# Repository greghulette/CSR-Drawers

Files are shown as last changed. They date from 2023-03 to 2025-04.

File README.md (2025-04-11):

# Horizontal Drawers for the COM-8 CSR Frame

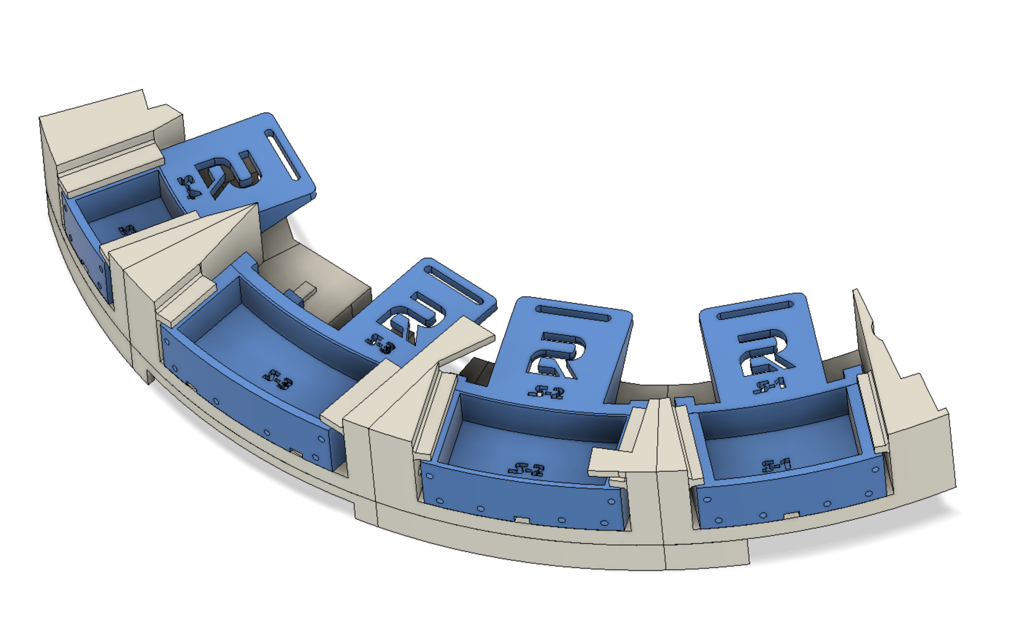
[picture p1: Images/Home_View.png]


 Drawers for the horizontal body panels.  I designed this for the COM-8 CSR frame.  It can be mounted to the frame, or to the skins.  

 I have included the STL's and the Fusion 360 file that you can open and edit anything you'd like.  Each drawer is split up into 4 parts.  
 1. Drawer Holder
 2. Drawer Body
 3. Drawer Servo Arm Attachment
 4. Skin Mount(Optional if you are mounting it to the skin instead of the frame)

 Hardware Needed:
 1. ES08MA II Servos - Qty:4 - [Link](https://www.amazon.com/dp/B07RRWYXL9?psc=1&ref=ppx_yo2ov_dt_b_product_details)  (HITEC HS65 will also work but the standard servo arms that come with them are not long enough.  You will need to get longer arms.Somthing longer than 20mm.  The hole needs to be about 18mm from the pivot point.)
 2. #0-80 5/8" Screws - Qty: 4
 3. #0-80 nuts - Qty: 8
 4. M3x10mm screws - Qty: 6
 5. M3 pressed/heated inserts - Qty: 6  (I also use thse to mount to my frame so I used 11 in total)
 6. 10x5x2mm neodynium N48 Magnets - Qty: 88 - [Link](https://www.amazon.com/dp/B0B6PBXBVJ?psc=1&ref=ppx_yo2ov_dt_b_product_details)
 7. M3x10 tapered screws - Qty: 5 (Only used if you are using the pressed inserts to mount the drawers to the frame)
 8. #4-40 1/2" tapered flat head screw (optional for skirt mount) - Qty 7
 9. #4-40 Lock nuts (optional for skirt mount) - Qty 7

I cut the longest servo arm that came with the servos.  This is the doublesided one.  I cut one side of it off.  I then drilled out the middle hole with a 1/16" drill bit to allow the bolt to go through.  

I put 2 nuts on each of the #0-80 screws and tightened them against each other to prevent the nut from coming loose.  
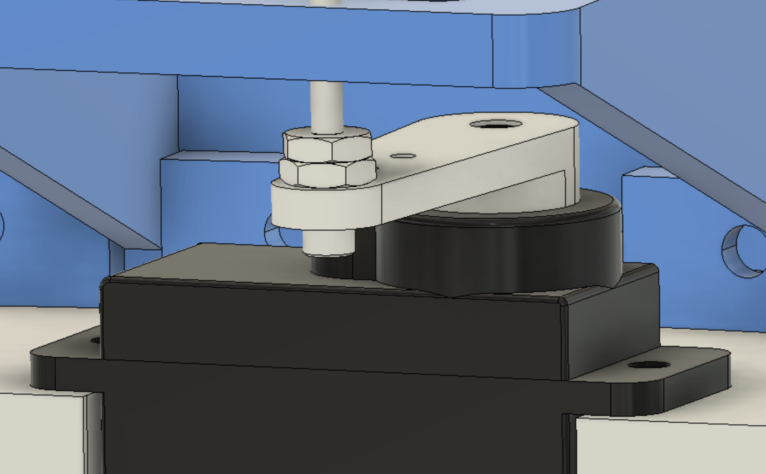
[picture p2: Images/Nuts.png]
Nuts


I used a soldering iron and pressed in the inserts to the side of each holder.  
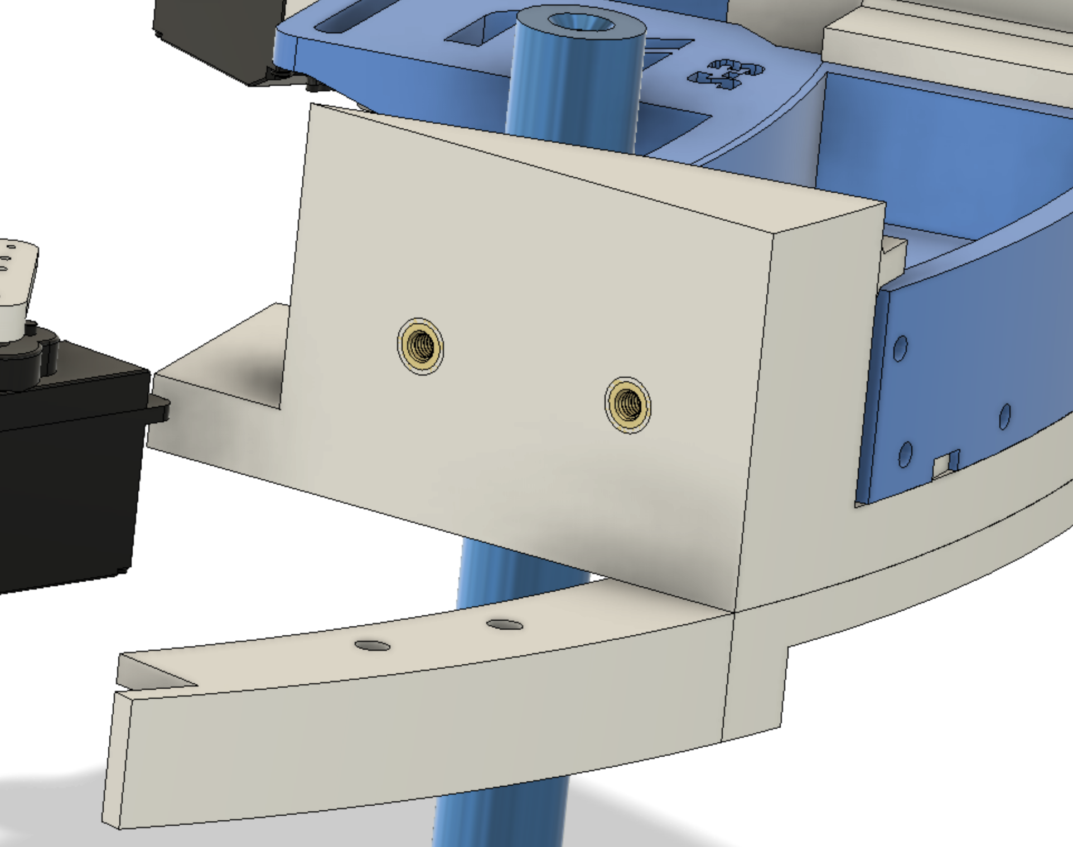
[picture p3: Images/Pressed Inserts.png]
Inserts


I then sanded the sides of each of the holders to make sure they sit flush with each other. Sometimes the pressing of the inserts leaves extra plastic stickup up and any if the sides aren't completely flush, it can cause the alignment to be off.  

You can then screw them together with the M3x10 screws(Not the tapered head ones)
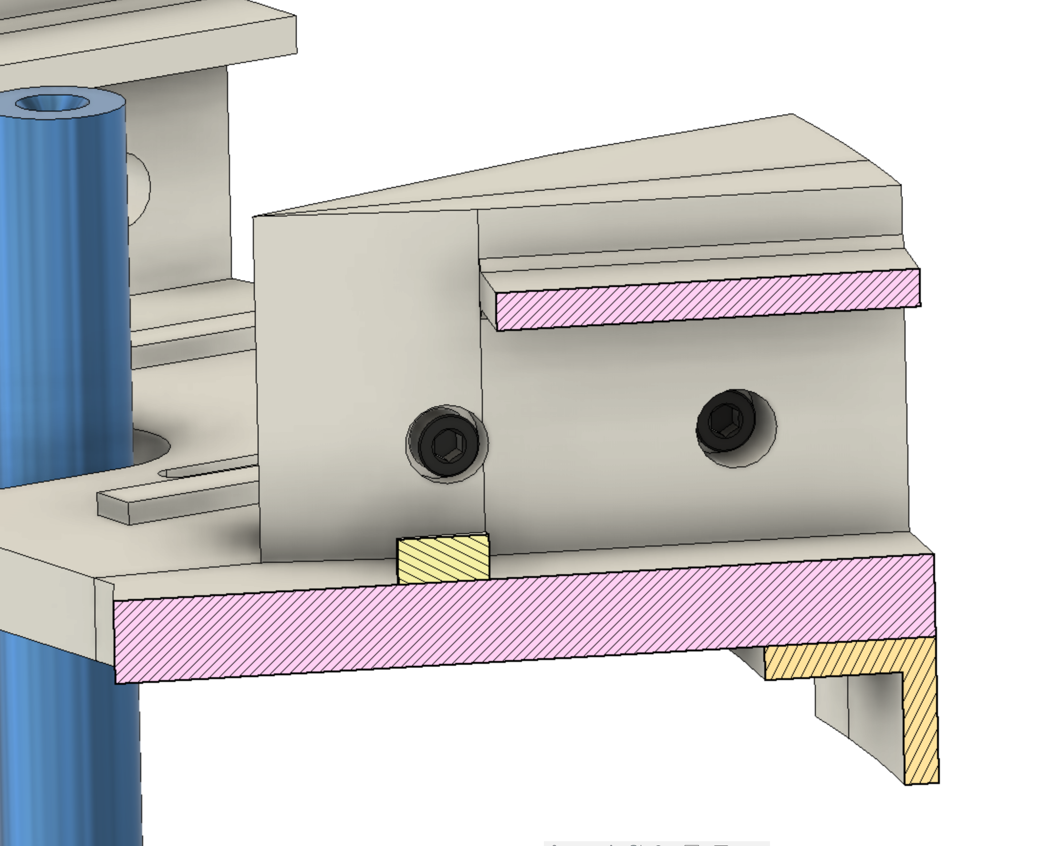
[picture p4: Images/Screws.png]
screws


I sanded the bottom of the drawrers and the top of the holders where the drawers sit on and slide to make sure the drawers slide smoothly.  With 3D printing, the top layer is rarely very smooth and likely has some variations.
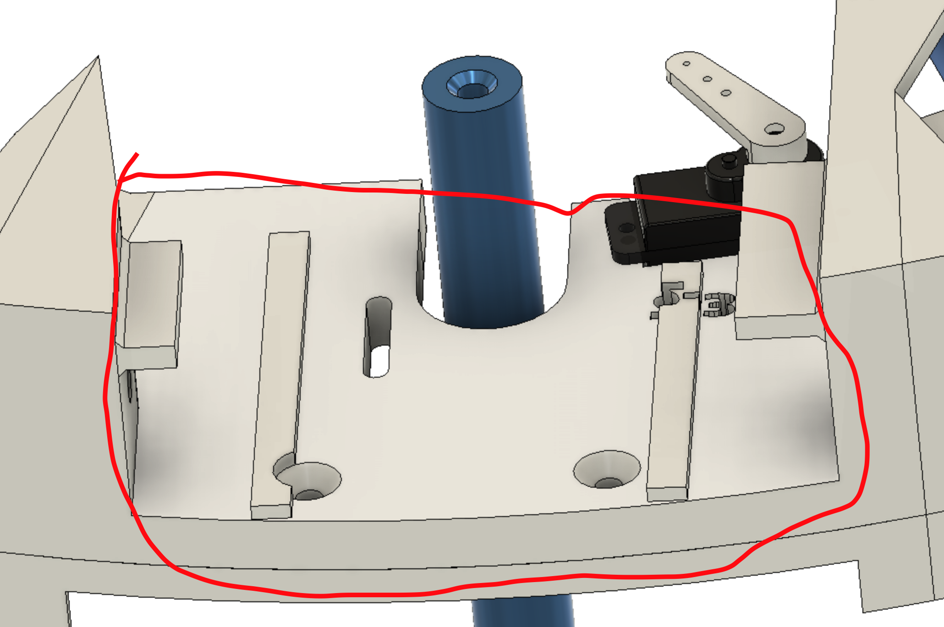
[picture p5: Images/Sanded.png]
sanded


I sanded the bottom of the drawer guides on the holders that stick out to prevent the drawers from lifting up.
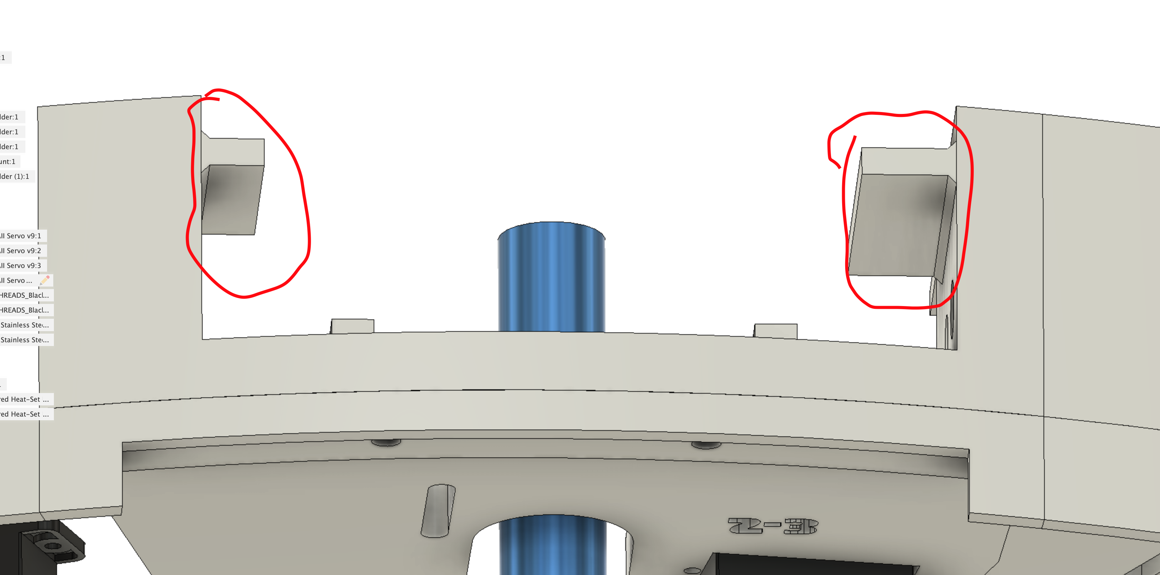
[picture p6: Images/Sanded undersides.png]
Sanded Undersides


THere are holes in the drawers behind the magnets for 2 purposes.  1 is to allow you to get the magnets out if you need to by poking it out from the back, and the 2nd is to allow a place for the glue to go when gluing in the magnets.  I found it easier to put all the magnets in the servo arm attachement first.  Then I placed the magnets for the body onto the magnets in the servo arm attachment and push them in into the body and twised the servo arm attachment away leaving the magnets with the correct polarity in the drawer body.  This helped not only assure the polarity is correct, but also helped me insert the magnets without twisting them.

## Installing on the frame

This seciton is going to sound like I'm rambling on, but this is the way I did it.  

I started off by removing the skins and all the utility arm risers/center vent holder from the frame.  This left me with enough room to get a drill in there later. I then put th skins back on and I measured about .25" spacing from the outer skin and cut that out on each of the 4 drawer openeings to start.  I then took the skins off and cut out that opening.  I installed the skins again and clamped in the assembled drawer mounts, without the drawers in them.  I tried to align it up as best I could to allow it to where I want it to.  There is a little room for side to side alignement.  I then filed the openings until I could slide the drawers in and out without hitting anything.  Once that was done,  took off the skins again and drilled a 1/16" pilot hole through the frame and into the part of the drawer holder that toughes the middle ring of the frame.  I then took off the drawer assembly and drill a larger hole to allow me to press in the heated inserts.  I then also drill out the hole in the frame to allow an M3 screw to go through it, then I tapered that hole in the frame to allow the screw to sit fluch with the frame.  Once that's all  done, you can put it all back together.  You want to put the utility arm carrier/Center vent holder back first since the screws will not be accesible once the drawer assembly is on.  

## Thanks to Doc Snyder and Matt Hobbs for the inspiration for these drawers.

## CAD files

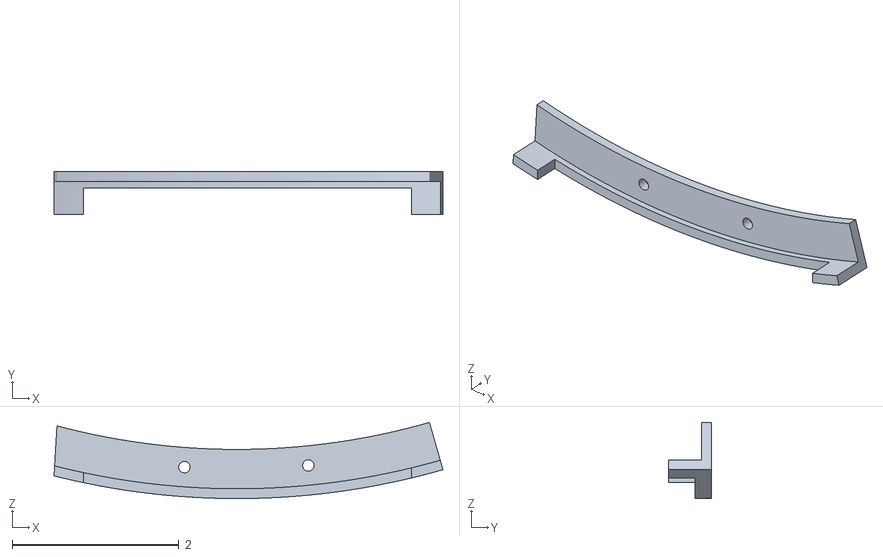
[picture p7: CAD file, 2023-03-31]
STL:3MF/S-3 Skin Mount.stl
4.67 x 0.512 x 0.915

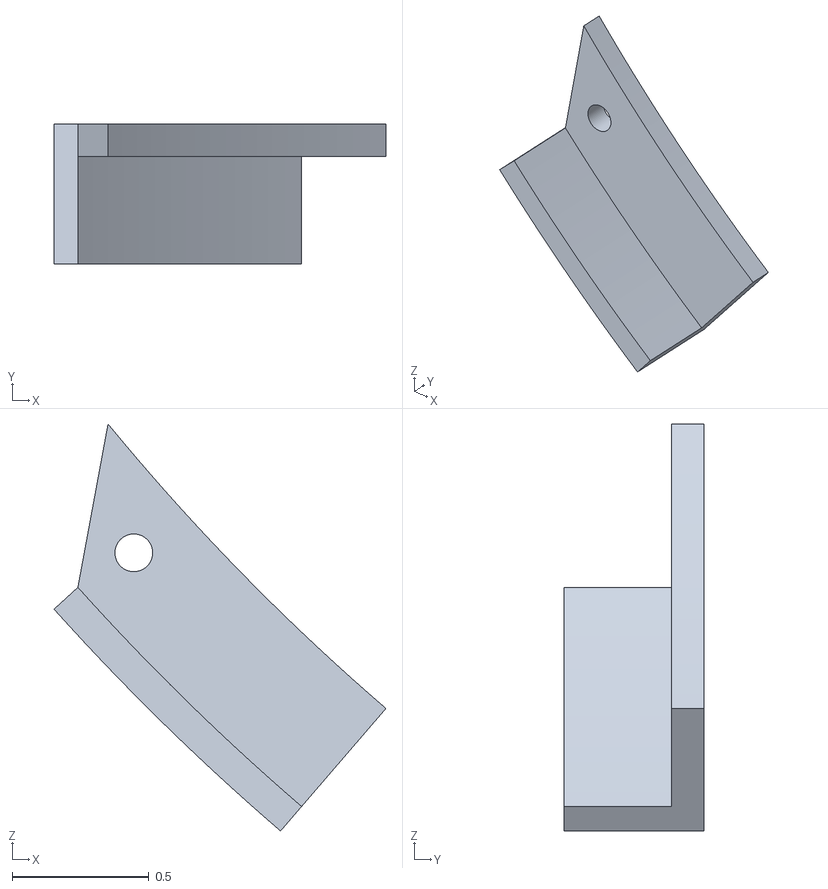
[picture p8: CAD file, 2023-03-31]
STL:3MF/S-1 Skin Mount.stl
1.21 x 0.512 x 1.49

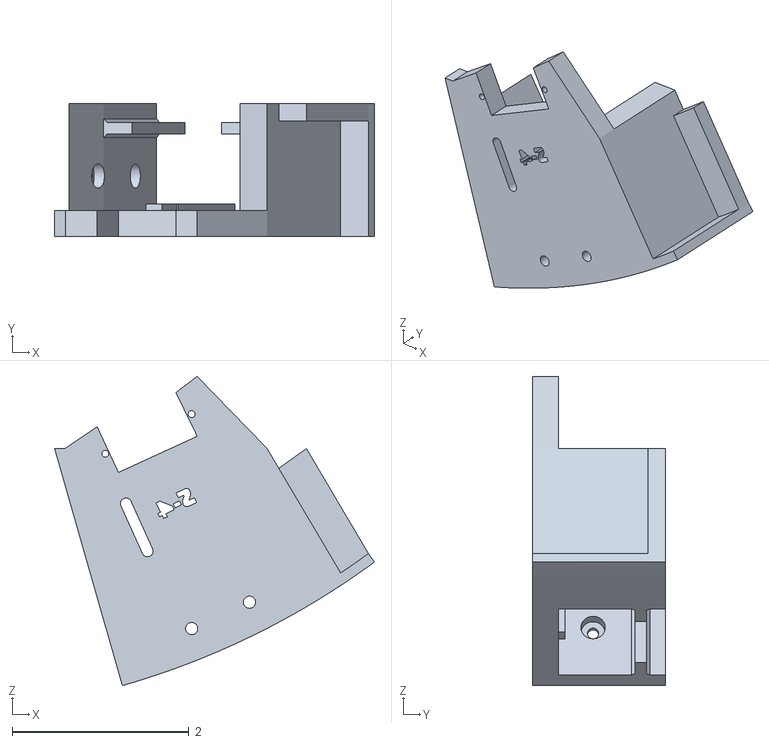
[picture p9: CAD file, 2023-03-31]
STL:3MF/S-4 Drawer Holder.stl
3.62 x 1.50 x 3.50

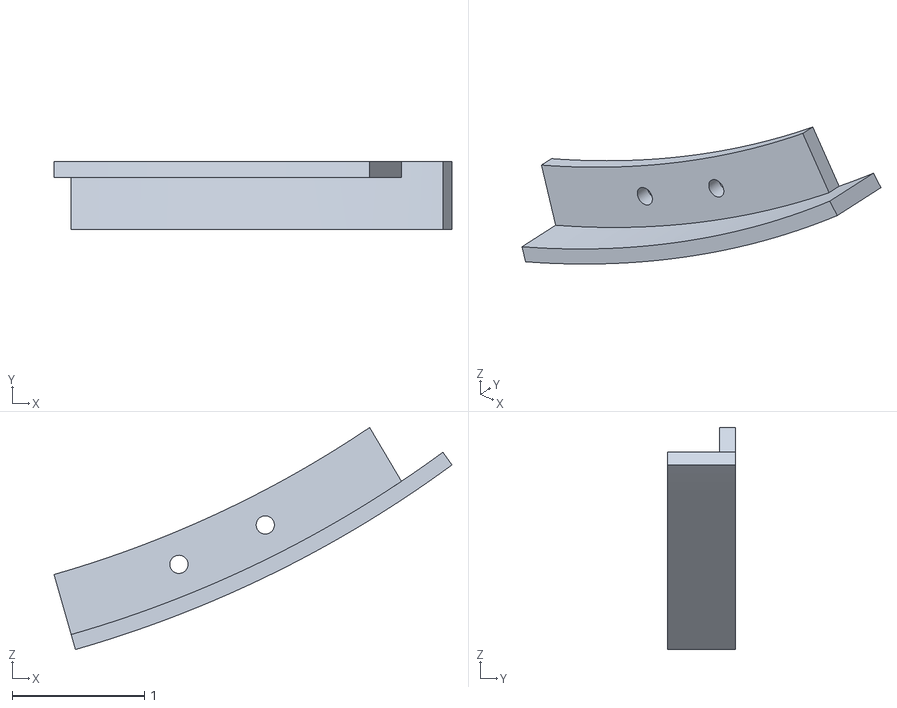
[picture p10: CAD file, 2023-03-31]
STL:3MF/S-4 Skin Mount.stl
3.01 x 0.512 x 1.68

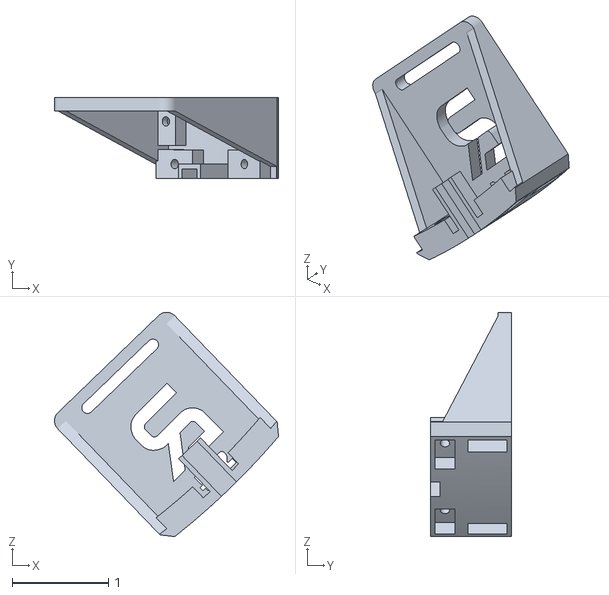
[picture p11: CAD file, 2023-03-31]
STL:3MF/S-4 Drawer Servo Arm Attachment.stl
2.33 x 0.841 x 2.34

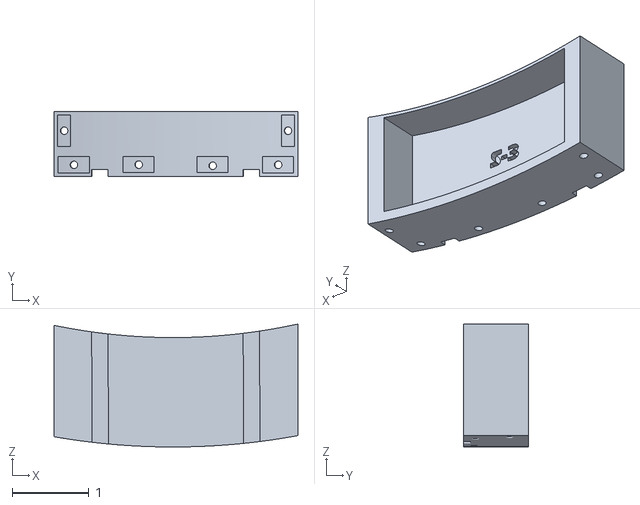
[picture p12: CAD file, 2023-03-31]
STL:3MF/S-3 Drawer Body.stl
3.17 x 0.841 x 1.60

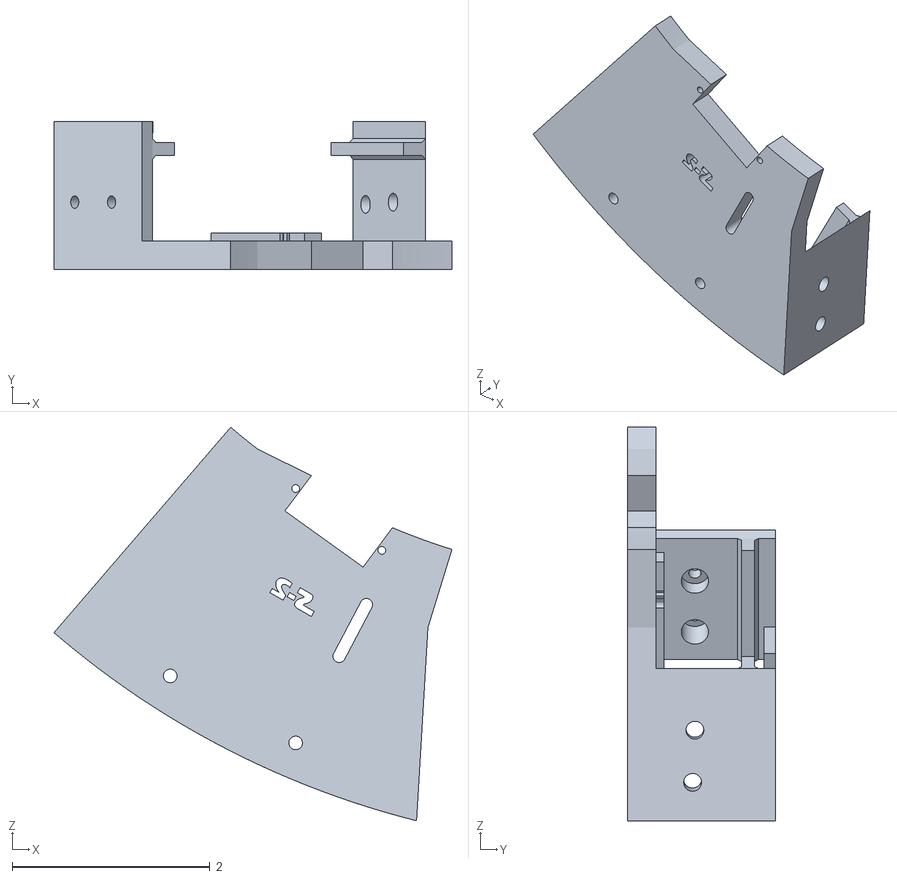
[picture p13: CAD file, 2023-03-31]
STL:3MF/S-2 Drawer Holder.stl
4.03 x 1.50 x 3.99

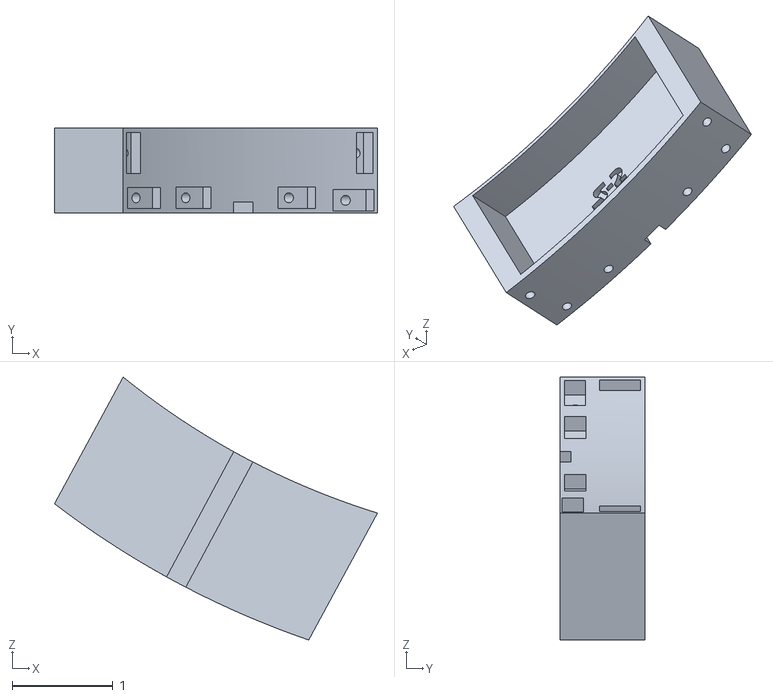
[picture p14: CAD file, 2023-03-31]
STL:3MF/S-2 Drawer Body.stl
3.21 x 0.841 x 2.61

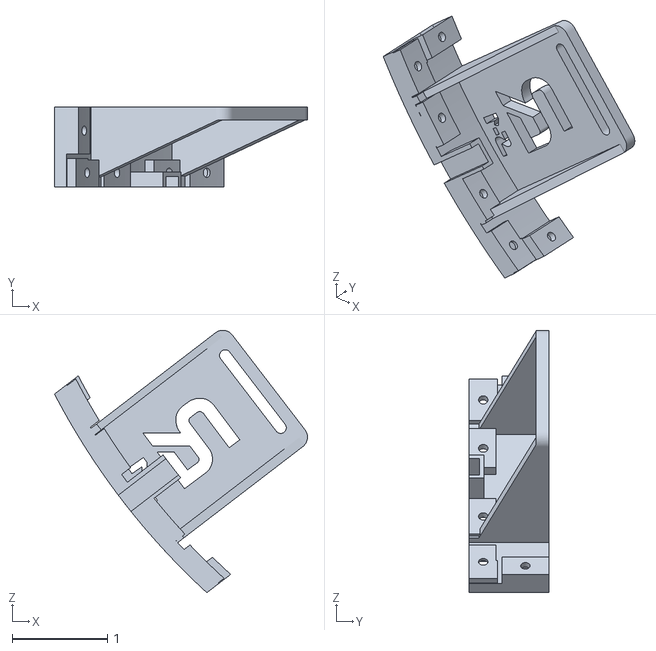
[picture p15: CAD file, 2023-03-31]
STL:3MF/S-1 Drawer Servo Arm Attachment.stl
2.66 x 0.841 x 2.76

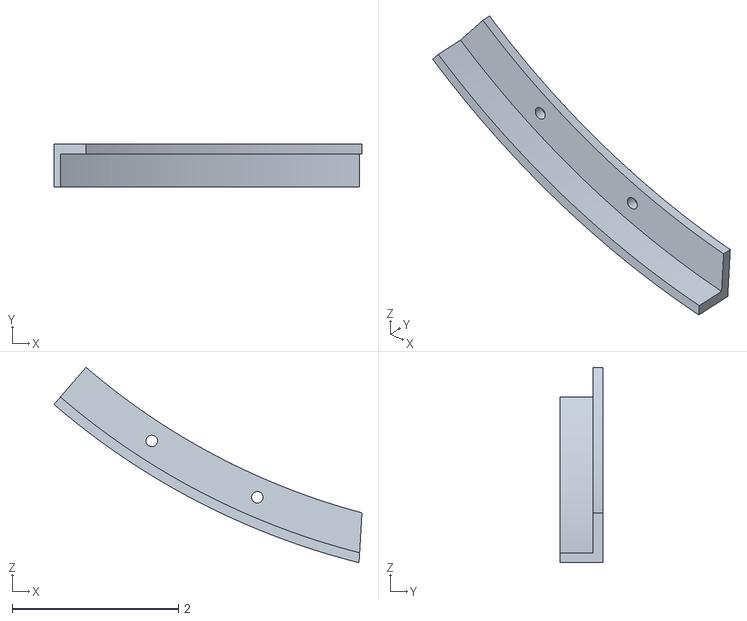
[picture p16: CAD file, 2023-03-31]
STL:3MF/S-2 Skin Mount.stl
3.71 x 0.512 x 2.35

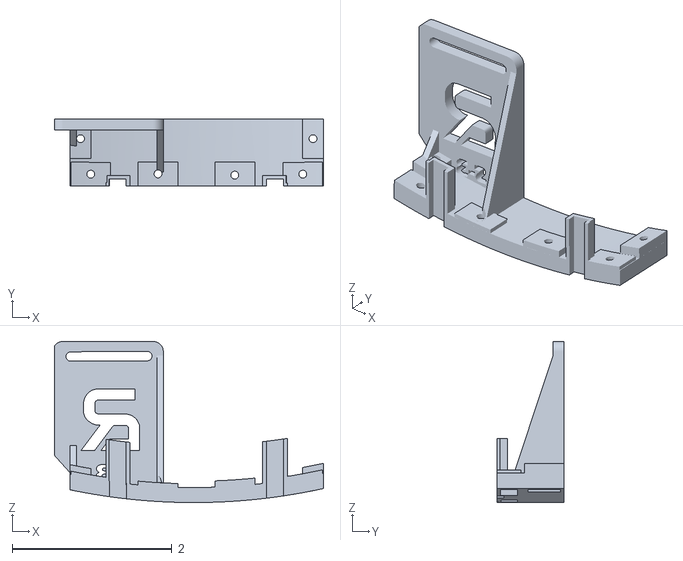
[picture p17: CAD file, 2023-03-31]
STL:3MF/S-3 Drawer Servo Arm Attachement.stl
3.37 x 0.841 x 2.02

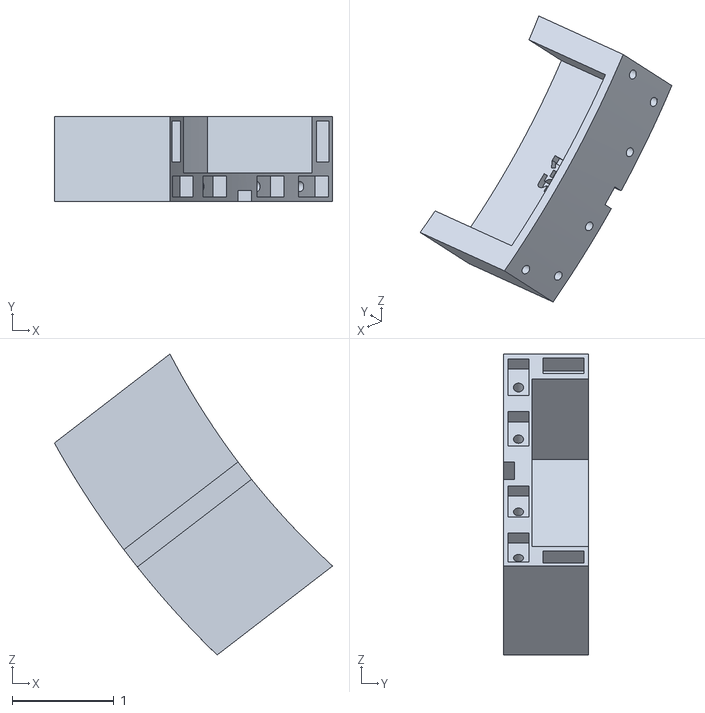
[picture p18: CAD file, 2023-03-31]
STL:3MF/S-1 Drawer Body.stl
2.74 x 0.841 x 2.96

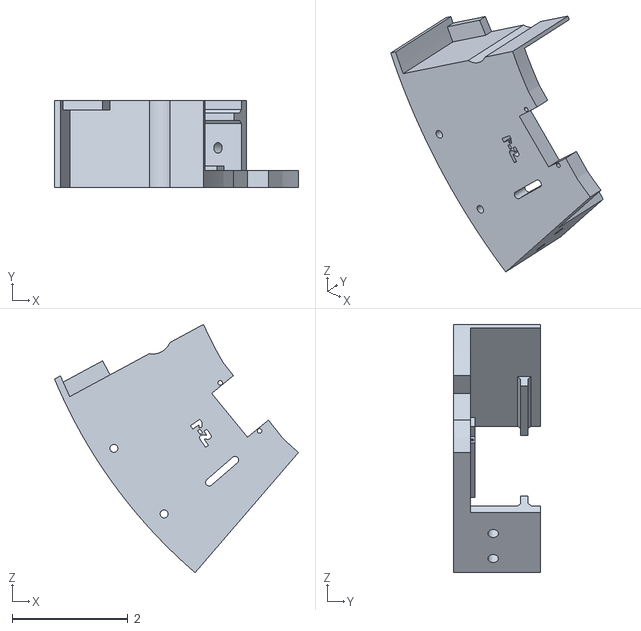
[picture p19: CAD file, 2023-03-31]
STL:3MF/S-1 Drawer Holder.stl
4.22 x 1.50 x 4.30

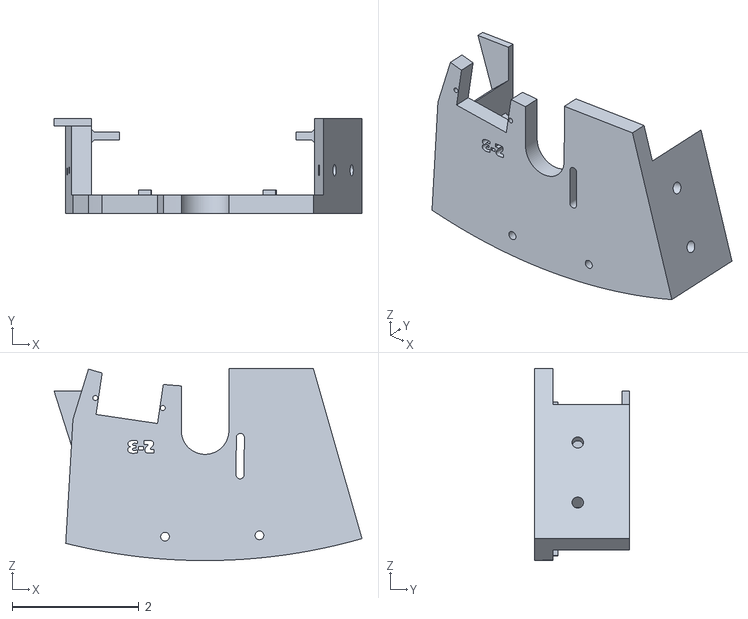
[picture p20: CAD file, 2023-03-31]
STL:3MF/S-3 Drawer Holder.stl
4.86 x 1.50 x 3.03

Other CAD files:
STL:3MF/S-2 Drawer Servo Arm Attachment .stl
STL:3MF/S-4 Drawer Body.stl

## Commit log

2023-03-31 Initial Upload
    [S-1 Drawer Body.stl, S-1 Drawer Holder.stl, S-1 Drawer Servo Arm Attachment.stl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]
2023-03-31 Update Drawers COM-8 CSR Frame.f3z
